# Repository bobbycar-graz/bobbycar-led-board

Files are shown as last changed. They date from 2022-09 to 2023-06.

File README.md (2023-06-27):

# bobbycar-led-board
A PCB designed for controlling lights on the bobbycar

## Features
- [ ] Control via CAN-Bus
- [ ] Webinterface
- [x] WS2812-like connector (5V-Data-GND, mr30)
- [ ] Two FET-switched DC connectors (xt30)
- [x] Current sensor to measure Power usage
- [x] VBAT voltage measurement
- [x] 5V voltage measurement (LED + Control Circuit)
- [x] SHT30 Temperature + Humidity Sensor

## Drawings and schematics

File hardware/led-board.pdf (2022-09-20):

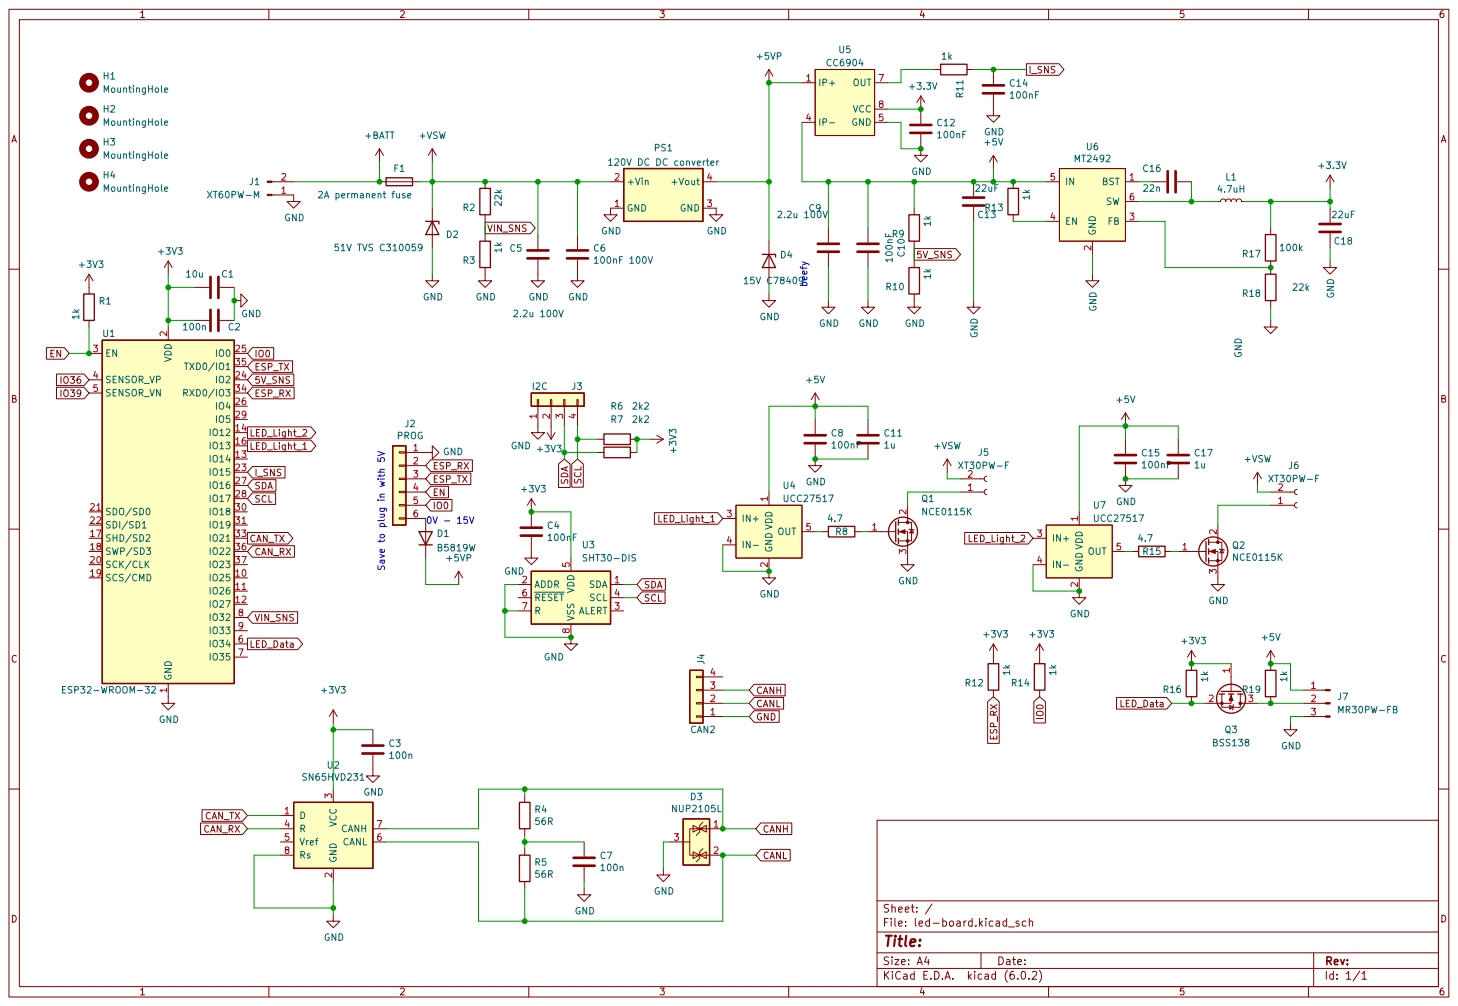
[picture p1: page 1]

2 SCK/CLK 20 SDO/SD0 21 SDI/SD1 22

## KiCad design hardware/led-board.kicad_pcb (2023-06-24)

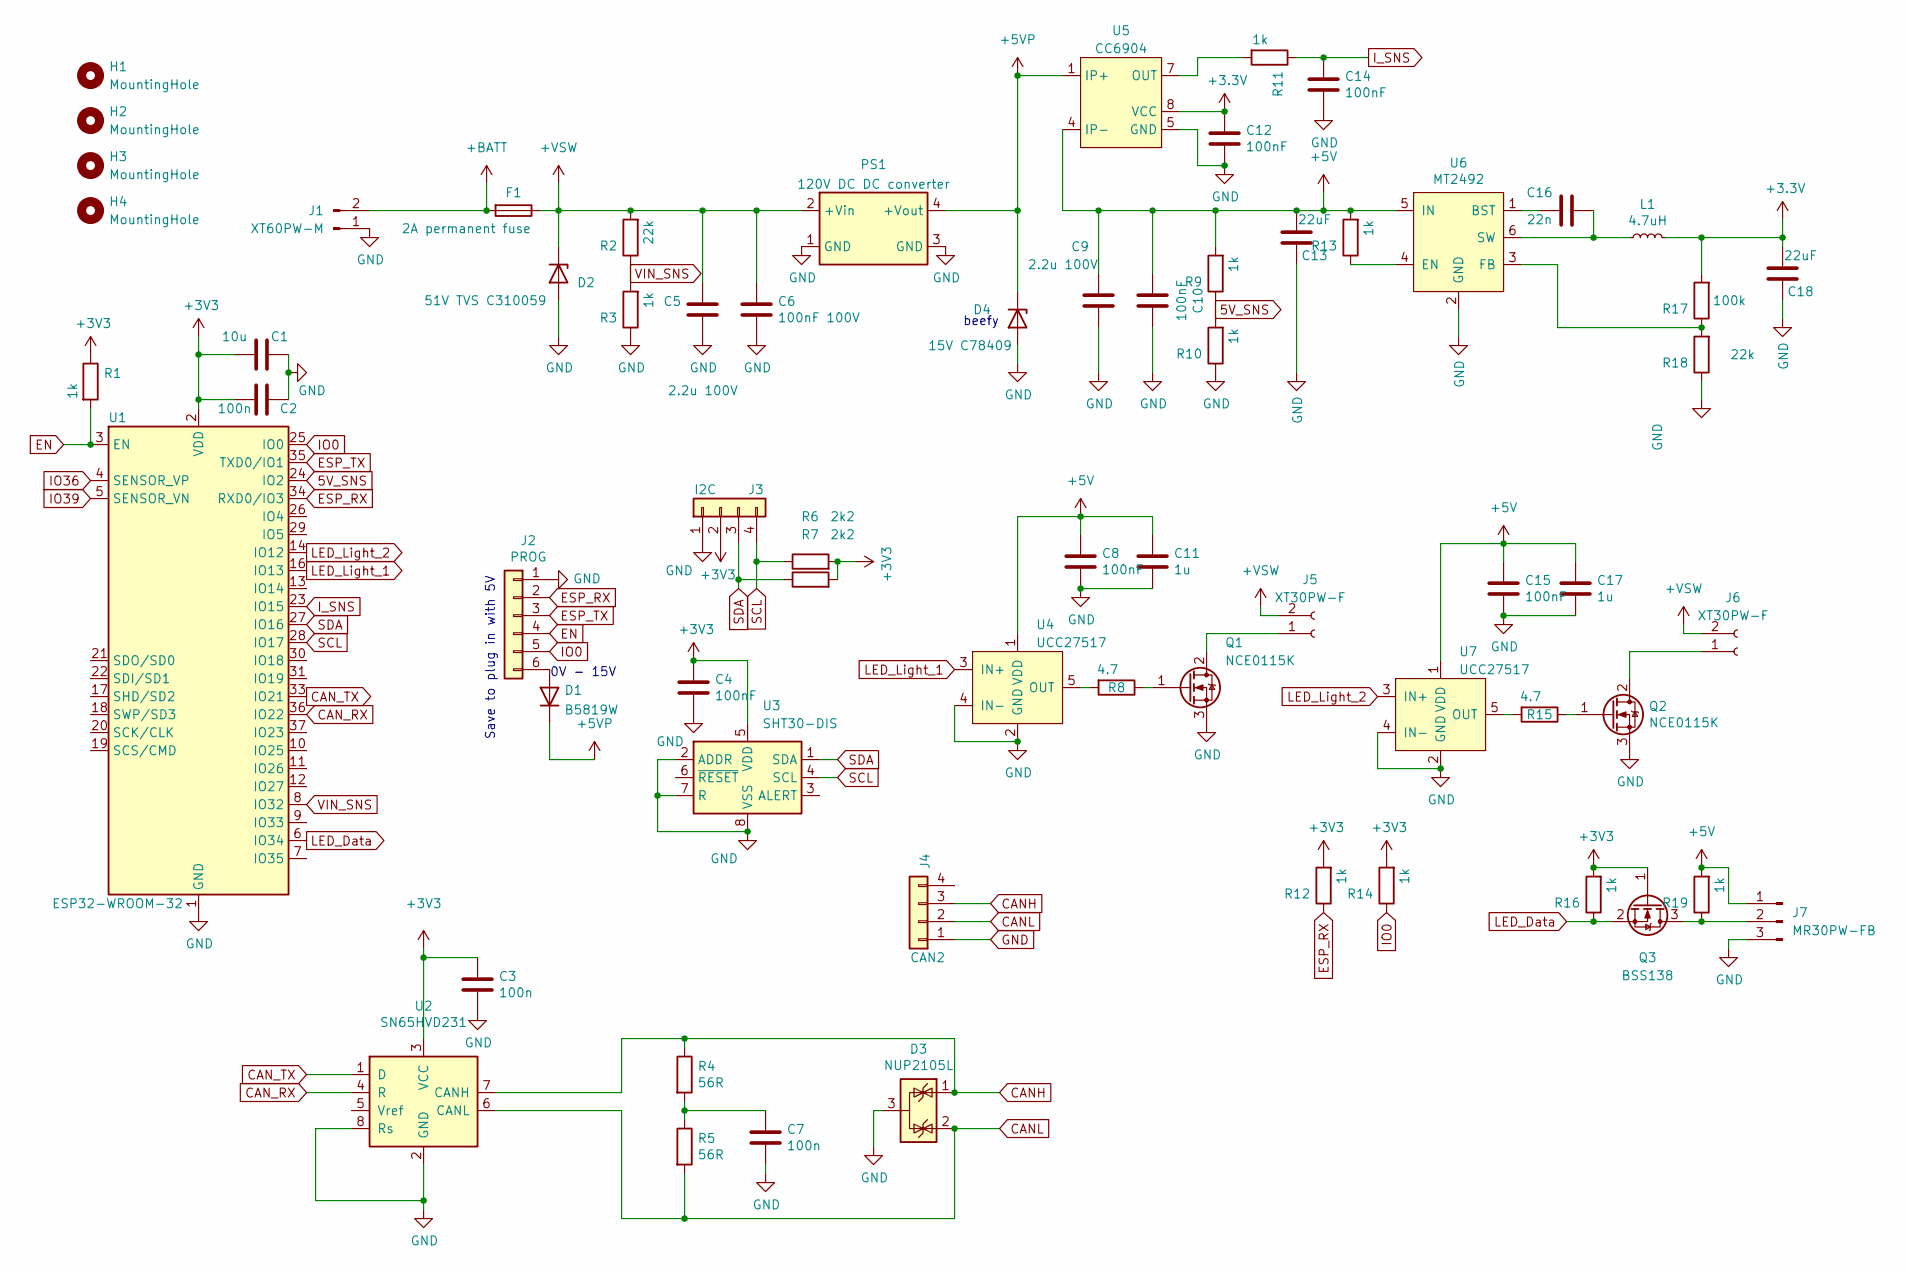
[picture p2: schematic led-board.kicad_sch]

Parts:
C1: 10u; C_0603_1608Metric; LCSC C19702
C2, C3, C7: 100n; C_0603_1608Metric; LCSC C14663
C4, C8, C10, C12, C14, C15: 100nF; C_0603_1608Metric; LCSC C14663
C5, C9: 2.2u 100V; C_1210_3225Metric; LCSC C76685
C6: 100nF 100V; C_0603_1608Metric; LCSC C113803
C11, C17: 1u; C_0805_2012Metric; LCSC C28323
C13, C18: 22uF; C_0805_2012Metric; LCSC C45783
C16: 22n; C_0603_1608Metric; LCSC C21122
D1: B5819W; D_SOD-123; LCSC Part # C8598
D2: 51V TVS C310059; D_SMC; LCSC C10374
D3: NUP2105L; SOT-23; LCSC C284104
D4: 15V C78409; D_SMB; LCSC C78409
F1: 2A permanent fuse; Fuse_1206_3216Metric; LCSC C182310
H1, H2, H3, H4: MountingHole; MountingHole_3.2mm_M3_DIN965_Pad
J1: XT60PW-M; Amass_XT60PW-M; LCSC C98732
J2: PROG; JST_XH_B6B-XH-A_1x06_P2.50mm_Vertical; LCSC Part # C144397
J3: I2C; JST_SH_SM04B-SRSS-TB_1x04-1MP_P1.00mm_Horizontal; LCSC C160404
J4: CAN2; JST_XH_B4B-XH-A_1x04_P2.50mm_Vertical; LCSC C144395
J5, J6: XT30PW-F; AMASS_XT30PW-F_1x02_P2.50mm_Horizontal
J7: MR30PW-FB; AMASS_MR30PW-FB_1x03_P3.50mm_Horizontal
L1: 4.7uH; L_5040; LCSC C354606
PS1: 120V DC DC converter; Converter_DCDC_120V
Q1, Q2: NCE0115K; TO-252-2; LCSC C108637
Q3: BSS138; SOT-23; LCSC C112239
R1, R3, R9, R10, R11, R12, R13, R14, R16, R19: 1k; R_0603_1608Metric; LCSC C21190
R2, R18: 22k; R_0603_1608Metric; LCSC C31850
R4, R5: 56R; R_0603_1608Metric; LCSC C25196
R6, R7: 2k2; R_0603_1608Metric; LCSC C4190
R8, R15: 4.7; R_1206_3216Metric; LCSC C17937
R17: 100k; R_0603_1608Metric; LCSC C25803
U1: ESP32-WROOM-32; LCSC C701343
U2: SN65HVD231; SOIC-8_3.9x4.9mm_P1.27mm; LCSC C30530
U3: SHT30-DIS; Sensirion_DFN-8-1EP_2.5x2.5mm_P0.5mm_EP1.1x1.7mm; LCSC C77361
U4, U7: UCC27517; SOT-23-5; LCSC C99395
U5: CC6904; SOIC-8_3.9x4.9mm_P1.27mm; LCSC C469389
U6: MT2492; SOT-23-6; LCSC C89358

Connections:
5V_SNS: R9.1, R10.2, U1.24 (IO2)
+5V: C8.1, C9.1, C10.2, C11.1, C13.2, C15.1, C17.1, J7.1, R9.2, R13.2, R19.2, U4.1 (VDD), U5.3 (IP-), U5.4 (IP-), U6.5 (IN), U7.1 (VDD)
+BATT: F1.2, J1.2
+VSW: C5.1, C6.1, D2.1 (K), F1.1, J5.2, J6.2, PS1.2 (+Vin), R2.2
CANH: D3.1 (K), J4.3, R4.1, U2.7 (CANH)
CANL: D3.2 (K), J4.2, R5.2, U2.6 (CANL)
CAN_RX: U1.36 (IO22), U2.4 (R)
CAN_TX: U1.33 (IO21), U2.1 (D)
EN: J2.4, R1.2, U1.3 (EN)
ESP_RX: J2.2, R12.1, U1.34 (RXD0/IO3)
ESP_TX: J2.3, U1.35 (TXD0/IO1)
GND: C1.1, C2.1, C3.2, C4.2, C5.2, C6.2, C7.2, C8.2, C9.2, C10.1, C11.2, C12.2, C13.1, C14.2, C15.2, C17.2, C18.1, D2.2 (A), D3.3 (A), D4.2 (A), J1.1, J2.1, J3.1, J4.1, J7.3, PS1.1 (GND), PS1.3 (GND), Q1.3 (S), Q2.3 (S), R3.1, R10.1, R18.1, U1.1 (GND), U1.15 (GND), U1.38 (GND), U1.39 (GND), U2.2 (GND), U2.8 (Rs), U3.2 (ADDR), U3.7 (R), U3.8 (VSS), U3.9 (VSS), U4.2 (GND), U4.4 (IN-), U5.5 (GND), U6.2 (GND), U7.2 (GND), U7.4 (IN-)
IO0: J2.5, R14.1, U1.25 (IO0)
IO36: U1.4 (SENSOR_VP)
IO39: U1.5 (SENSOR_VN)
I_SNS: C14.1, R11.1, U1.23 (IO15)
LED_Data: Q3.2 (S), R16.1, U1.6 (IO34)
LED_Light_1: U1.16 (IO13), U4.3 (IN+)
LED_Light_2: U1.14 (IO12), U7.3 (IN+)
unnamed: C7.1, R4.2, R5.1
unnamed: C16.1, L1.1, U6.6 (SW)
unnamed: C16.2, U6.1 (BST)
unnamed: D1.2 (A), J2.6
unnamed: J5.1, Q1.2 (D)
unnamed: J6.1, Q2.2 (D)
unnamed: J7.2, Q3.3 (D), R19.1
unnamed: Q1.1 (G), R8.1
unnamed: Q2.1 (G), R15.1
unnamed: R8.2, U4.5 (OUT)
unnamed: R11.2, U5.7 (OUT)
unnamed: R13.1, U6.4 (EN)
unnamed: R15.2, U7.5 (OUT)
unnamed: R17.1, R18.2, U6.3 (FB)
SCL: J3.4, R6.1, U1.28 (IO17), U3.4 (SCL)
SDA: J3.3, R7.1, U1.27 (IO16), U3.1 (SDA)
VIN_SNS: R2.1, R3.2, U1.8 (IO32)

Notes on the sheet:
Save to plug in with 5V
beefy
0V - 15V

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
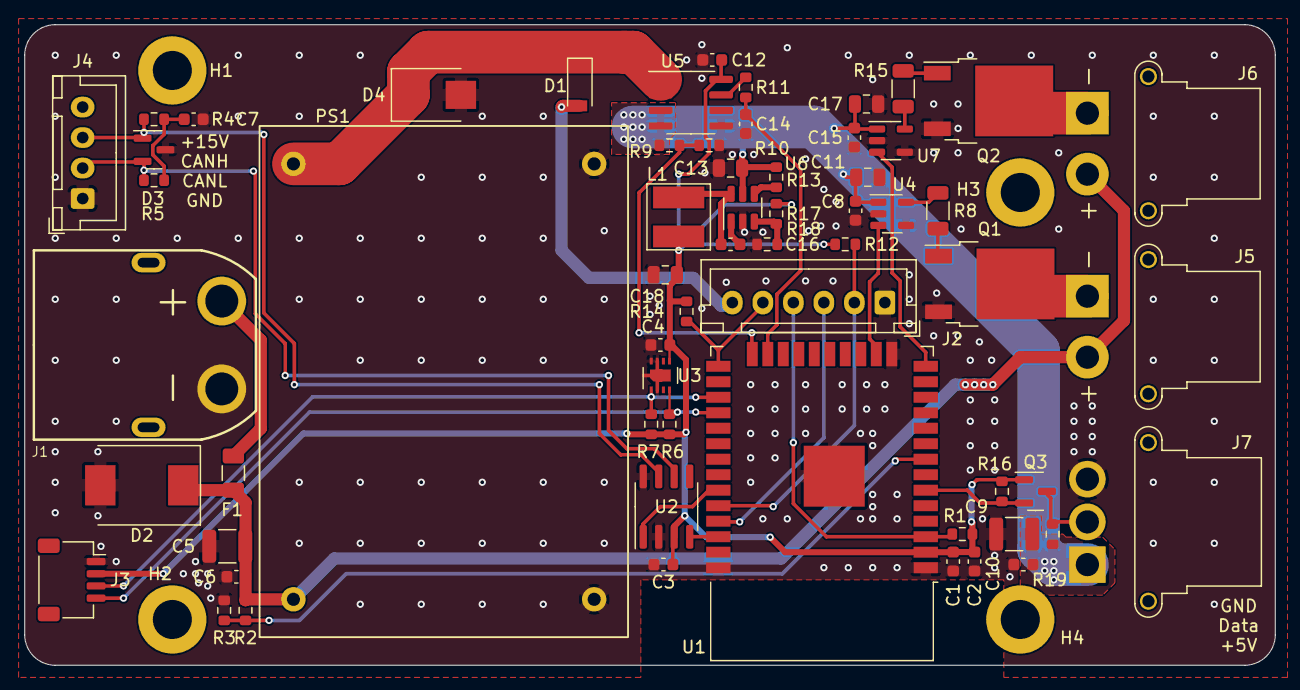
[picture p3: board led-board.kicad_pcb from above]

Board: 2 copper layers, 102.5 x 52.5 mm, 65 parts (0 on the bottom side), 36 nets.

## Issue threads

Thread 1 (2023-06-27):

LED Data connected to wrong Pin

CommanderRedYT, 2023-06-27:
Before it was on a Input-Only pin, now for dev PCB we moved it to GPIO26

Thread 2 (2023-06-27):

Move 5V & Current senor pin

CommanderRedYT, 2023-06-27:
- Move 5V sens pin to GPIO33 (adc2 -> adc1)
- Move Current sens pin to GPIO35 (adc2 -> adc1)

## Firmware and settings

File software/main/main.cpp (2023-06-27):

constexpr const char * const TAG = "BOBBYCAR-LED-BOARD";

// esp-idf includes
#include <esp_log.h>
#include <tickchrono.h>

// 3rdparty lib includes
#include <espchrono.h>

// local includes
#include "taskmanager.h"
#include "measurements.h"

using namespace std::chrono_literals;

extern "C" [[noreturn]] void app_main()
{
    for (auto &task : schedulerTasks)
    {
        ESP_LOGI(TAG, "Init task %s", task.name());
        task.setup();
    }

    while (true)
    {
        for (auto &task : schedulerTasks)
        {
            task.loop();
        }

        const auto now = espchrono::millis_clock::now();
        static auto last = now;

        if (espchrono::ago(last) > 100ms)
        {
            last = now;
            ESP_LOGI(TAG, "V5V_RAW: %i, V5V_VALUE: %f - VBAT_RAW: %i, VBAT_VALUE: %f - I_RAW: %i, I_VALUE: %f, Temperature: %f, Humidity: %f",
                     measure::measure_v5v.raw,
                     measure::measure_v5v.value,
                     measure::measure_vbat.raw,
                     measure::measure_vbat.value,
                     measure::measure_current.raw,
                     measure::measure_current.value,
                    measure::measure_sht3x.temperature,
                    measure::measure_sht3x.humidity
            );
        }

        vTaskDelay(1);
    }
}

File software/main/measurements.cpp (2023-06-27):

constexpr const char * const TAG = "MEASUREMENTS";
#include "measurements.h"

// esp-idf includes
#include <esp_log.h>
#include <esp_adc/adc_oneshot.h>
#include <esp_adc/adc_cali.h>
#include <esp_adc/adc_cali_scheme.h>
#include <driver/i2c.h>

// 3rdparty lib includes
#include <espchrono.h>
#include <sht3x.h>

// local includes
#include "pins.h"

/*
constexpr pin_t BAT_VOLTAGE_SENSOR = 32;
constexpr uint8_t BAT_VOLTAGE_RATIO = 23; // 22k + 1k voltage divider

constexpr pin_t V5V_VOLTAGE_SENSOR = 33;
constexpr uint8_t V5V_VOLTAGE_RATIO = 2; // 1k + 1k voltage divider

constexpr pin_t CURRENT_SENSOR = 35;
constexpr uint8_t CURRENT_SENSOR_RATIO = 132; // mV/A
*/

using namespace std::chrono_literals;

namespace measure {

AdcMeasurementResult measure_v5v;
AdcMeasurementResult measure_vbat;
AdcMeasurementResult measure_current;
SHT3XMeasurementResult measure_sht3x;

namespace {

bool adc_calibration_init(adc_unit_t unit, adc_channel_t channel, adc_atten_t atten, adc_cali_handle_t *out_handle)
{
    adc_cali_handle_t handle = nullptr;
    esp_err_t ret = ESP_FAIL;
    bool calibrated{false};

#if ADC_CALI_CURVE_FITTING_SUPPORTED
    if (!calibrated)
    {
        ESP_LOGI(TAG, "calibration scheme version is %s", "Curve Fitting");
        adc_cali_curve_fitting_config_t cali_config = {
            .unit_id = unit,
            .chan = channel,
            .atten = atten,
            .bitwidth = ADC_BITWIDTH_DEFAULT,
        };
        ret = adc_cali_create_scheme_curve_fitting(&cali_config, &handle);
        if (ret == ESP_OK)
        {
            calibrated = true;
        }
    }
#endif

#if ADC_CALI_SCHEME_LINE_FITTING_SUPPORTED
    if (!calibrated)
    {
        ESP_LOGI(TAG, "calibration scheme version is %s", "Line Fitting");
        adc_cali_line_fitting_config_t cali_config = {
            .unit_id = unit,
            .atten = atten,
            .bitwidth = ADC_BITWIDTH_DEFAULT,
        };
        ret = adc_cali_create_scheme_line_fitting(&cali_config, &handle);
        if (ret == ESP_OK)
        {
            calibrated = true;
        }
    }
#endif

    *out_handle = handle;

    if (ret != ESP_OK)
    {
        ESP_LOGE(TAG, "ADC calibration failed: %s", esp_err_to_name(ret));
    }

    return calibrated;
}

// unit handle
adc_oneshot_unit_handle_t adc1_handle{nullptr};

// cali handles
adc_cali_handle_t adc1_cali_chan5_handle{nullptr}; // V5V
adc_cali_handle_t adc1_cali_chan4_handle{nullptr}; // VBAT
adc_cali_handle_t adc1_cali_chan7_handle{nullptr}; // I

// do calibration flags
bool do_calibration_chan5{false};
bool do_calibration_chan4{false};
bool do_calibration_chan7{false};

bool i2c_initialized{false};

} // namespace

void init()
{
    adc_oneshot_unit_init_cfg_t adc1_unit_config = {
        .unit_id = ADC_UNIT_1,
    };

    if (const auto res = adc_oneshot_new_unit(&adc1_unit_config, &adc1_handle); res != ESP_OK)
    {
        ESP_LOGE(TAG, "Error initializing ADC: %s", esp_err_to_name(res));
        return;
    }

    adc_oneshot_chan_cfg_t adc1_channel_config = {
        .atten = ADC_ATTEN_DB_11,
        .bitwidth = ADC_BITWIDTH_12,
    };

    // V5V - pin 33 => ADC1_CHANNEL_5
    if (const auto res = adc_oneshot_config_channel(adc1_handle, ADC_CHANNEL_5, &adc1_channel_config); res != ESP_OK)
    {
        ESP_LOGE(TAG, "Error configuring ADC channel 5: %s", esp_err_to_name(res));
        return;
    }

    // VBAT - pin 32 => ADC1_CHANNEL_4
    if (const auto res = adc_oneshot_config_channel(adc1_handle, ADC_CHANNEL_4, &adc1_channel_config); res != ESP_OK)
    {
        ESP_LOGE(TAG, "Error configuring ADC channel 4: %s", esp_err_to_name(res));
        return;
    }

    // I - pin 35 => ADC1_CHANNEL_7
    if (const auto res = adc_oneshot_config_channel(adc1_handle, ADC_CHANNEL_7, &adc1_channel_config); res != ESP_OK)
    {
        ESP_LOGE(TAG, "Error configuring ADC channel 7: %s", esp_err_to_name(res));
        return;
    }

    do_calibration_chan5 = adc_calibration_init(ADC_UNIT_1, ADC_CHANNEL_5, ADC_ATTEN_DB_11, &adc1_cali_chan5_handle);
    do_calibration_chan4 = adc_calibration_init(ADC_UNIT_1, ADC_CHANNEL_4, ADC_ATTEN_DB_11, &adc1_cali_chan4_handle);
    do_calibration_chan7 = adc_calibration_init(ADC_UNIT_1, ADC_CHANNEL_7, ADC_ATTEN_DB_11, &adc1_cali_chan7_handle);

    ESP_LOGI(TAG, "ADC configured");

    i2c_config_t i2c_config = {
        .mode = I2C_MODE_MASTER,
        .sda_io_num = I2C_SDA,
        .scl_io_num = I2C_SCL,
        .sda_pullup_en = GPIO_PULLUP_ENABLE,
        .scl_pullup_en = GPIO_PULLUP_ENABLE,
        .master = {
            .clk_speed = 100000,
        },
    };

    if (const auto res = i2c_param_config(I2C_NUM_0, &i2c_config); res != ESP_OK)
    {
        ESP_LOGE(TAG, "Error configuring I2C: %s", esp_err_to_name(res));
        return;
    }

    if (const auto res = i2c_driver_install(I2C_NUM_0, I2C_MODE_MASTER, 0, 0, 0); res != ESP_OK)
    {
        ESP_LOGE(TAG, "Error installing I2C driver: %s", esp_err_to_name(res));
        return;
    }

    i2c_initialized = true;

    ESP_LOGI(TAG, "I2C configured");
}
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

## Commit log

2022-09-20 Push of first board version
    [BOM-led-board.csv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]
2022-09-20 update of pdf schematic
    [led-board.kicad_sch]
2023-06-24 Preparations for Software
    [BOM-led-board.csv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]
2023-06-24 Added gitignore
    [BOM-led-board.csv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]
2023-06-25 Updated wrong pins
    [led-board.kicad_sch]
2023-06-27 Read out SHT30 sensor; preps for Ledstrip
